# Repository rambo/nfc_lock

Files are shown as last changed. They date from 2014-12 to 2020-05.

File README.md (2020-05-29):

nfc_lock
========

(more) secure electric lock with DESFire EV1 NFC tags

## libnfc and libfreefare

    sudo apt-add-repository ppa:christopher-hoskin/ppa
    sudo apt-get update
    sudo apt-get install libnfc5 libnfc-bin libnfc-pn53x-examples libnfc-examples
    sudo apt-get install libfreefare0 libfreefare-bin
    sudo apt-get install python-zmq python-yaml python-tornado

`python-yaml` and `python-tornado` can be installed to virtualenv (esp tornado might be better to install via pip even if not to virtualenv the deb pulls unneccessary dependencies), zmq will be painful to install via pip, use the system package.

### For compiling

For the C programs.

    sudo apt-get install libfreefare-dev libnfc-dev libssl-dev pkg-config libzmq-dev

### RasPi

All libraries should be part of normal releases now.

## Terms

  - Card (PICC in NXP terms): The DESFire EV1 chip+antenna in a package (fob, card, sticker...)
  - Pre-Personalization step: Where card default master key is changed and applications are defined.
  - Application: collection of files on the card, application can have multiple keys for various purposes
  - Provisioning (or personalization) step: Where a personalized card is issued to a card holder and the card (plus backing datababase) is updated with relevant info
  - Diversified key: Key that has been derived from a master key via the method described in NXP AN19022

## SQLite for keys

Create a test file `sqlite3 keys.db`:

    CREATE TABLE valid_tokens (value TEXT UNIQUE, type INTEGER, acl INTEGER, external_ids TEXT);
    CREATE TABLE revoked_tokens (value TEXT UNIQUE, type INTEGER);

Prepare some tags and insert their (real) UIDs to the grants and revokes

    INSERT INTO revoked_tokens VALUES ("04453069b21e80");
    INSERT INTO valid_tokens VALUES ("04212f69b21e80", 0, 1);

In reality you will generate this file based on your person registry (keep track of validity times etc there, then regenerate the keydb for the door).

## Hacking

Remember to valgrind your C programs (`valgrind -v --leak-check=yes  myprog args`) at the same time as you do general functionality testing.

### RasPi

It seems Valgrind does not (and will not) support some instructions we use to talk with the NFC chips, see (this stackoverflow)[valgrindworkaround] for a workaround.

[valgrindworkaround]: http://stackoverflow.com/questions/20066215/valgrind-unrecognizes-memcmp-instruction-in-raspberry-pi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

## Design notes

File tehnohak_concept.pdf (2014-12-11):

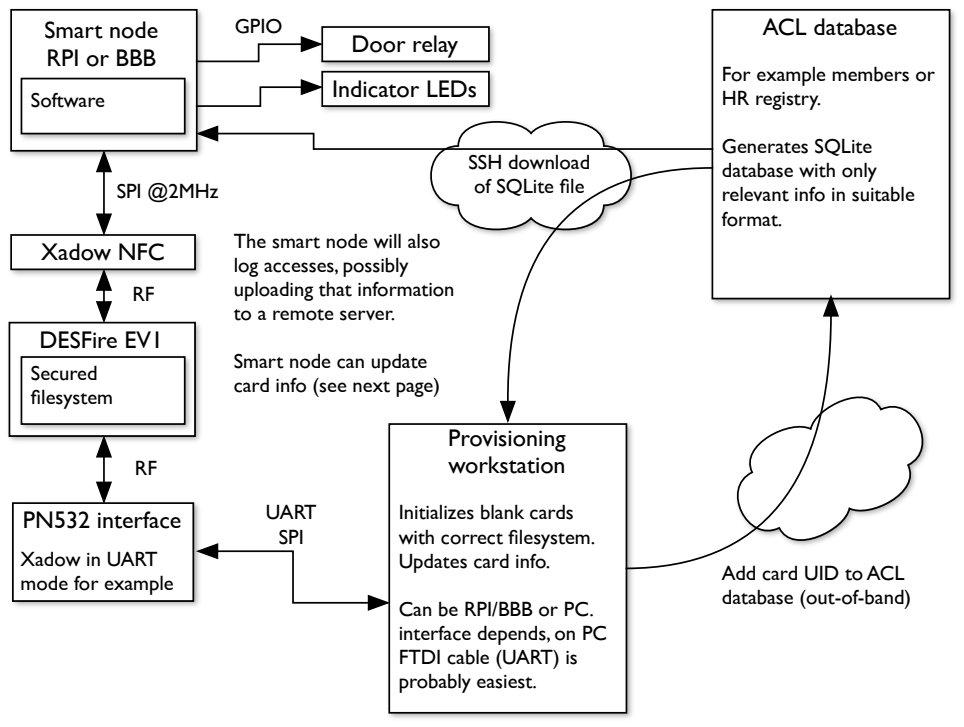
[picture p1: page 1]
Xadow NFC; SPI @2MHz; DESFire EV1 Secured filesystem; Door relay; GPIO; ACL database; Indicator LEDs; Provisioning workstation; UART SPI

Smart node
RPI or BBB
Software

For example members or
HR registry.

Generates SQLite
database with only
relevant info in suitable
format.

SSH download
of SQLite file

The smart node will also
log accesses, possibly
uploading that information
to a remote server.

Smart node can update
card info (see next page)

PN532 interface
Xadow in UART
mode for example

Initializes blank cards
with correct filesystem.
Updates card info.

Add card UID to ACL
database (out-of-band)

Can be RPI/BBB or PC.
interface depends, on PC
FTDI cable (UART) is
probably easiest.

# Card authentication

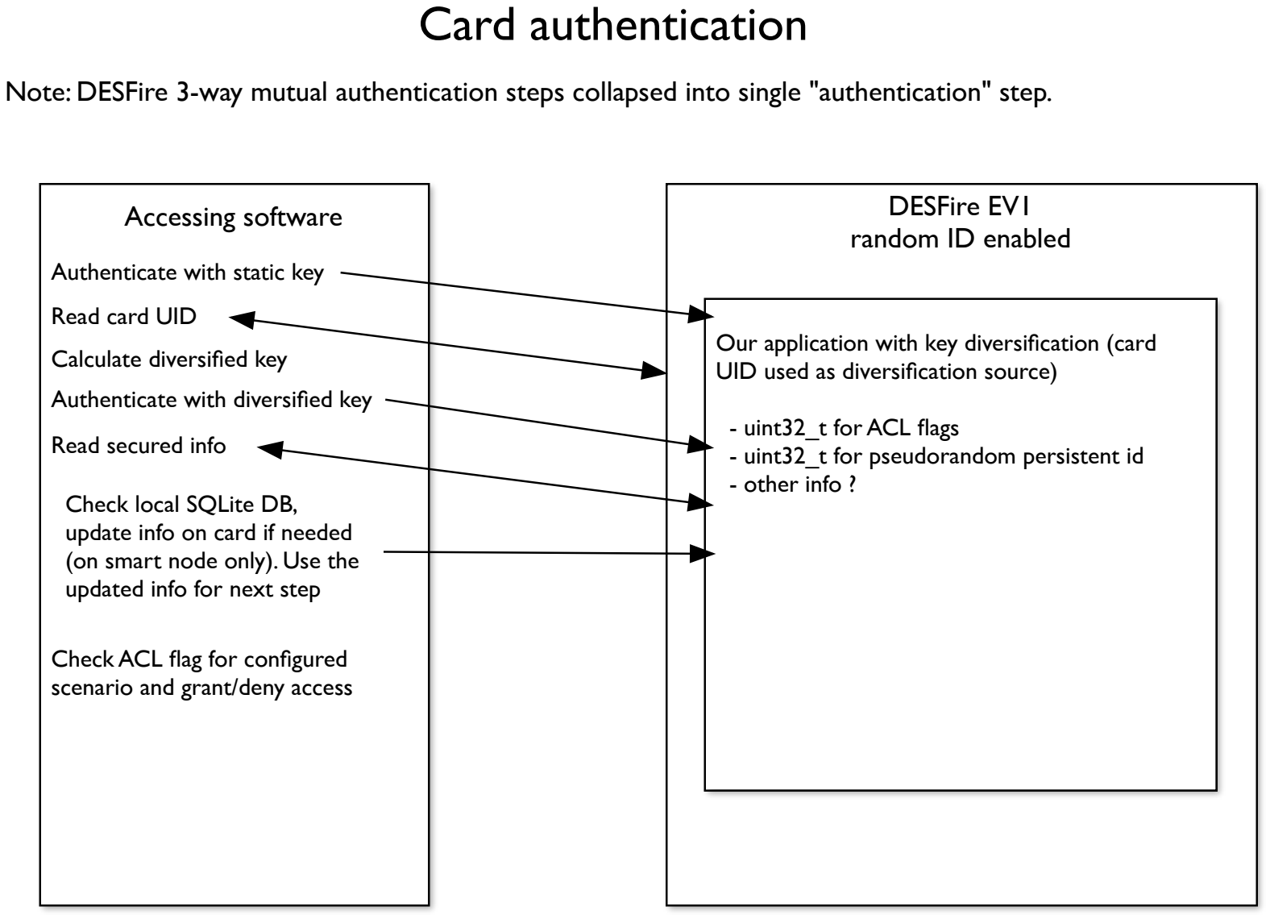
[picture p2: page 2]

Note: DESFire 3-way mutual authentication steps collapsed into single "authentication" step.

DESFire EV1
random ID enabled

Our application with key diversification (card UID used as diversification source)

- uint32_t for ACL flags
- uint32_t for pseudorandom persistent id
- other info ?

Accessing software

Authenticate with static key Read card UID
Calculate diversified key
Authenticate with diversified key Read secured info

Check local SQLite DB,
update info on card if needed (on smart node only). Use the updated info for next step

Check ACL flag for configured scenario and grant/deny access

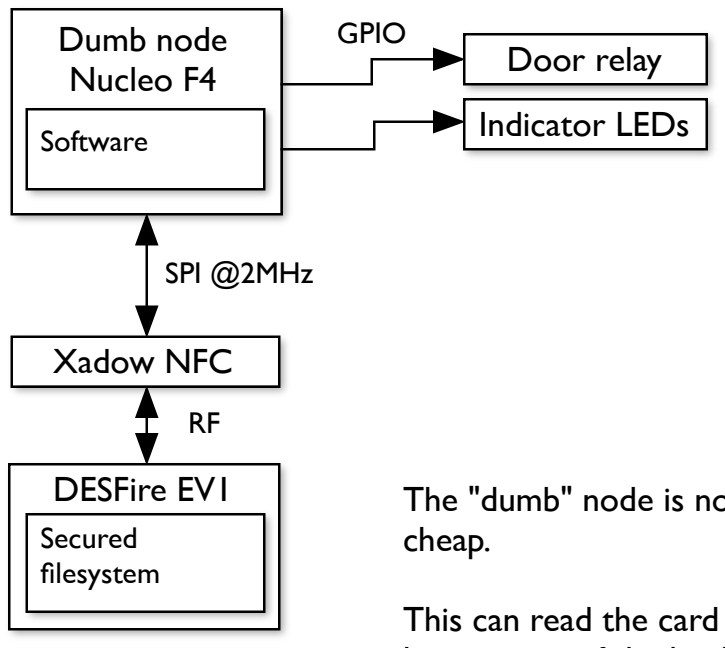
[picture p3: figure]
Dumb node Nucleo F4; Xadow NFC; SPI @2MHz; DESFire EV1; Software; Secured filesystem; Door relay; GPIO; Indicator LEDs; cheap.

The "dumb" node is not capable of running a full OS but the MCU is

This can read the card and check the ACL flag, but the node does not have a copy of the key/acl database or anything like that, it trusts that the smart node (which are at building entrances) will keep the flags updated.

It can do simple UDP broadcast of events (UID xxx granted/denied at node YYY) which the smart nodes can listen for (and log).

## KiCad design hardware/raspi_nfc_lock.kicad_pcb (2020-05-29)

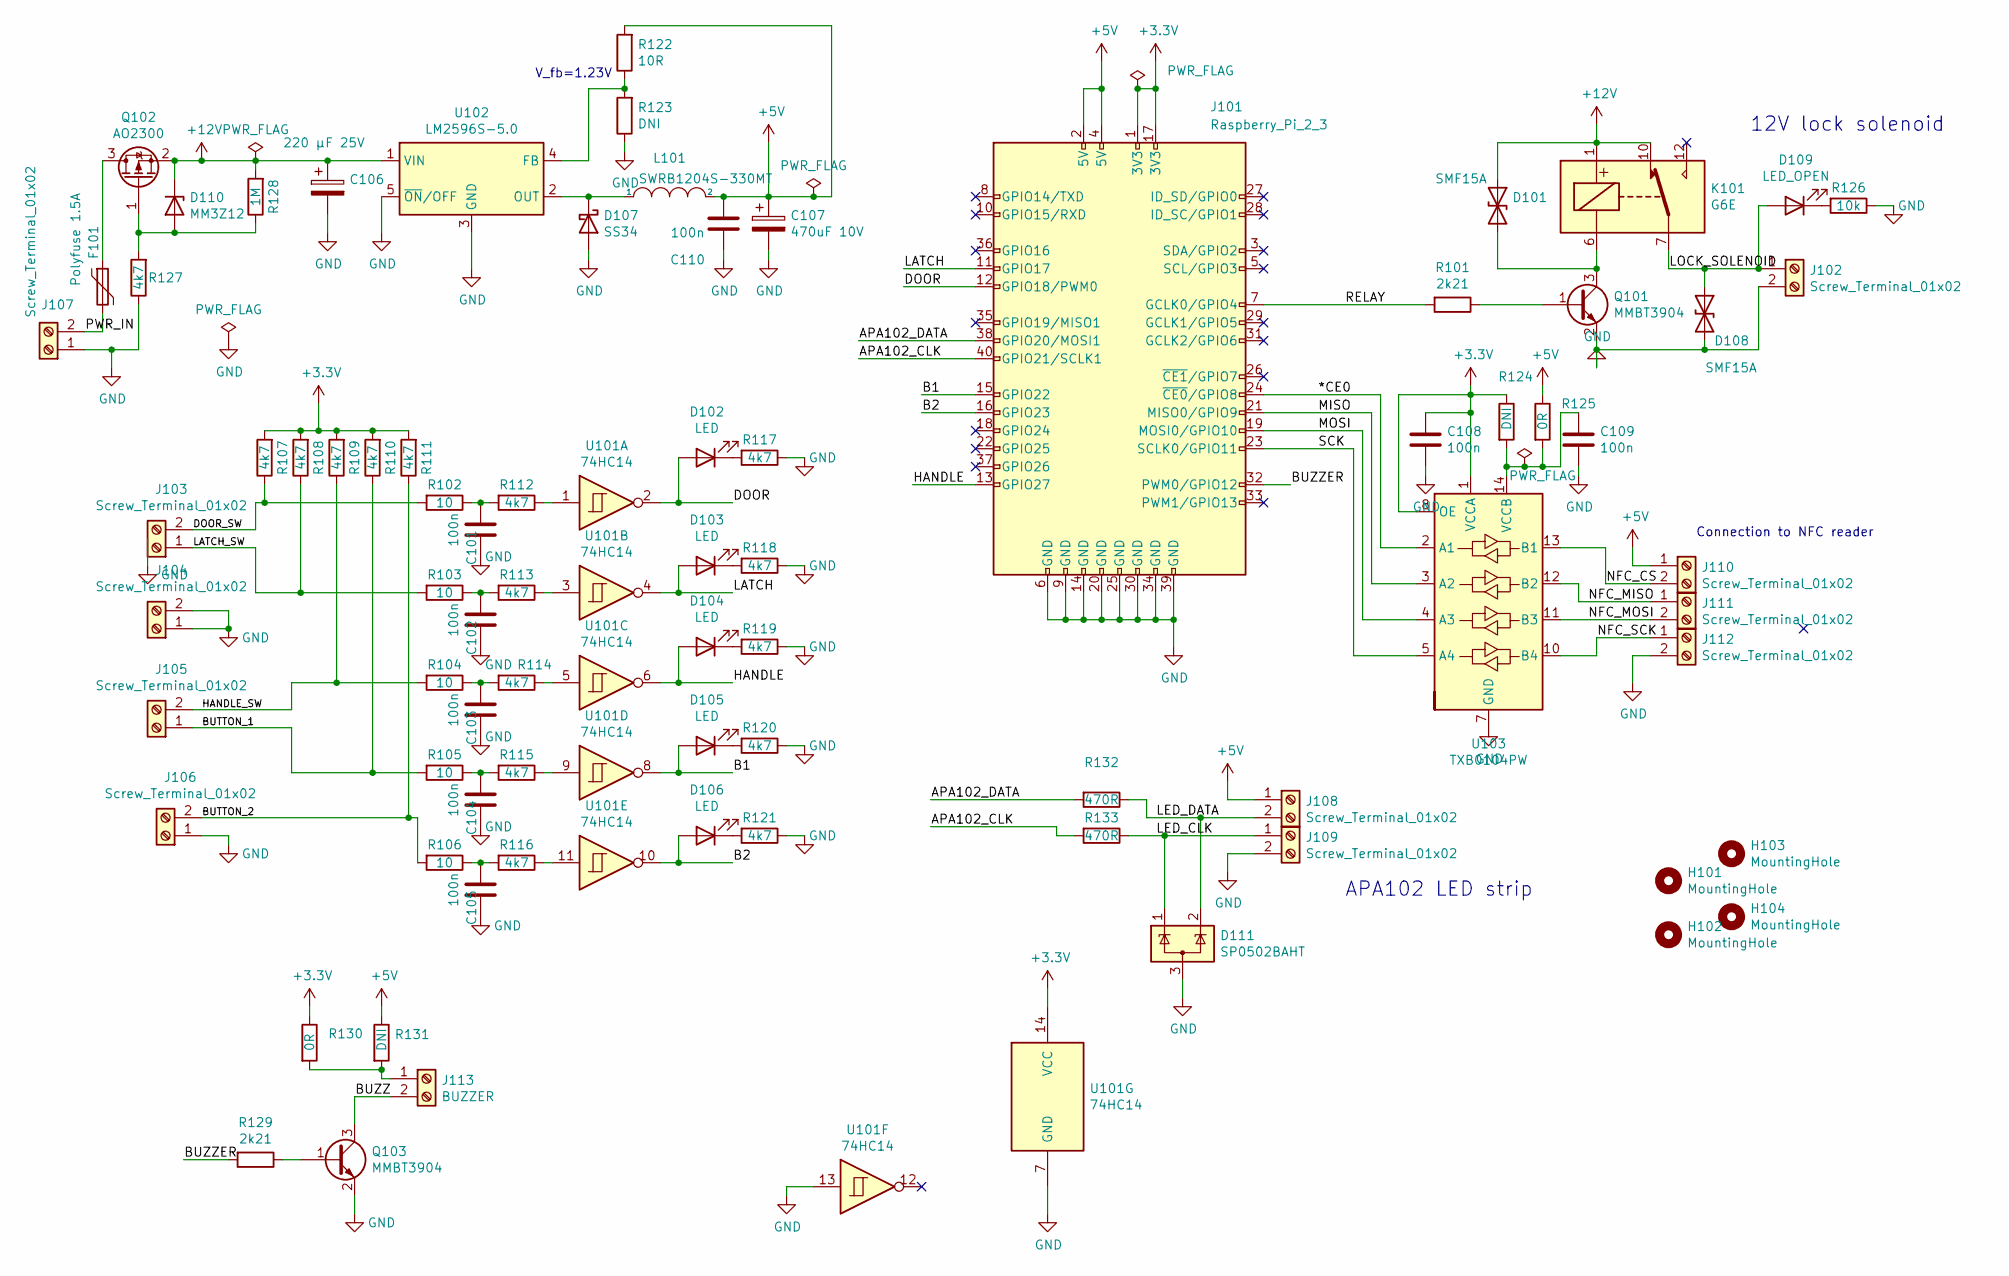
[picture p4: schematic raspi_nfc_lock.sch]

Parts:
C101, C102, C103, C104, C105, C108, C109: 100n; C_0603
C106: 220 μF 25V; CP_Elec_8x10
C107: 470uF 10V; CP_Elec_8x10.5
C110: 100n; C_1206
D101, D108: SMF15A; D_SOD-123
D102, D103, D104, D105, D106: LED; D_0603_1608Metric
D107: SS34; D_SMA
D109: LED_OPEN; D_0603_1608Metric
D110: MM3Z12; D_SOD-323
D111: SP0502BAHT; SOT-23
F101: Polyfuse 1.5A; Fuse_SMD2920
H101, H102, H103, H104: MountingHole; MountingHole_3.2mm_M3
J101: Raspberry_Pi_2_3; Pin_Header_Straight_2x20_Pitch2.54mm
J102, J103, J104, J105, J106, J107, J108, J109, J110, J111, J112: Screw_Terminal_01x02; TerminalBlock_Phoenix_MPT-0,5-2-2.54_1x02_P2.54mm_Horizontal
J113: BUZZER; TerminalBlock_Phoenix_MPT-0,5-2-2.54_1x02_P2.54mm_Horizontal
K101: G6E; Relay_SPDT_Omron_G6E
L101: SWRB1204S-330MT; L_12x12mm_H6mm
Q101, Q103: MMBT3904; SOT-23
Q102: AO2300; SOT-23
R101, R129: 2k21; R_0603
R102, R103, R104, R105, R106: 10; R_0603
R107, R108, R109, R110, R111, R112, R113, R114, R115, R116, R117, R118, R119, R120, R121, R127: 4k7; R_0603
R122: 10R; R_0603
R123, R124, R131: DNI; R_0603
R125, R130: 0R; R_0603
R126: 10k; R_0603
R128: 1M; R_0603
R132, R133: 470R; R_0603
U101: 74HC14; SOIC-14_3.9x8.7mm_P1.27mm
U102: LM2596S-5.0; TO-263-5_TabPin3
U103: TXB0104PW; TSSOP-14_4.4x5mm_P0.65mm

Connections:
+3V3: C108.1, J101.1 (3V3), J101.17 (3V3), R107.2, R108.2, R109.2, R110.2, R111.2, R124.1, R130.1, U101.14 (VCC), U103.1 (VCCA), U103.8 (OE)
+5V: C107.1, C110.2, J101.2 (5V), J101.4 (5V), J108.1, J110.1, L101.2, R122.2, R125.1, R131.1
+12V: C106.1, D101.1 (A1), D110.1 (K), K101.1, K101.10, Q102.2 (S), R128.2, U102.1 (VIN)
/*CE0: J101.24 (~CE0~/GPIO8), U103.2 (A1)
/APA102_CLK: J101.40 (GPIO21/SCLK1), R133.2
/APA102_DATA: J101.38 (GPIO20/MOSI1), R132.2
/B1: D105.2 (A), J101.15 (GPIO22), U101.8
/B2: D106.2 (A), J101.16 (GPIO23), U101.10
/BUTTON_1: J105.1, R105.2, R110.1
/BUTTON_2: J106.2, R106.2, R111.1
/BUZZ: J113.2, Q103.3 (C)
/BUZZER: J101.32 (PWM0/GPIO12), R129.2
/DOOR: D102.2 (A), J101.12 (GPIO18/PWM0), U101.2
/DOOR_SW: J103.2, R102.2, R107.1
/HANDLE: D104.2 (A), J101.13 (GPIO27), U101.6
/HANDLE_SW: J105.2, R104.2, R109.1
/LATCH: D103.2 (A), J101.11 (GPIO17), U101.4
/LATCH_SW: J103.1, R103.2, R108.1
/LED_CLK: D111.1 (K), J109.1, R133.1
/LED_DATA: D111.2 (K), J108.2, R132.1
/LOCK_SOLENOID: D108.1 (A1), D109.2 (A), J102.1, K101.7
/MISO: J101.21 (MISO0/GPIO9), U103.3 (A2)
/MOSI: J101.19 (MOSI0/GPIO10), U103.4 (A3)
/NFC_CS: J110.2, U103.13 (B1)
/NFC_MISO: J111.1, U103.12 (B2)
/NFC_MOSI: J111.2, U103.11 (B3)
/NFC_SCK: J112.1, U103.10 (B4)
/PWR_IN: F101.2, J107.2
/RELAY: J101.7 (GCLK0/GPIO4), R101.2
/SCK: J101.23 (SCLK0/GPIO11), U103.5 (A4)
GND: C101.1, C102.1, C103.1, C104.1, C105.1, C106.2, C107.2, C108.2, C109.2, C110.1, D107.2 (A), D108.2 (A2), D111.3 (A), J101.6 (GND), J101.9 (GND), J101.14 (GND), J101.20 (GND), J101.25 (GND), J101.30 (GND), J101.34 (GND), J101.39 (GND), J102.2, J104.1, J104.2, J106.1, J107.1, J109.2, J112.2, Q101.2 (E), Q103.2 (E), R117.1, R118.1, R119.1, R120.1, R121.1, R123.1, R126.1, R127.1, U101.7 (GND), U101.13, U102.3 (GND), U102.5 (~ON~/OFF), U103.7 (GND)
unnamed: C101.2, R102.1, R112.2
unnamed: C102.2, R103.1, R113.2
unnamed: C103.2, R104.1, R114.2
unnamed: C104.2, R105.1, R115.2
unnamed: C105.2, R106.1, R116.2
unnamed: C109.1, R124.2, R125.2, U103.14 (VCCB)
unnamed: D101.2 (A2), K101.6, Q101.3 (C)
unnamed: D102.1 (K), R117.2
unnamed: D103.1 (K), R118.2
unnamed: D104.1 (K), R119.2
unnamed: D105.1 (K), R120.2
unnamed: D106.1 (K), R121.2
unnamed: D107.1 (K), L101.1, U102.2 (OUT)
unnamed: D109.1 (K), R126.2
unnamed: D110.2 (A), Q102.1 (G), R127.2, R128.1
unnamed: F101.1, Q102.3 (D)
unnamed: J113.1, R130.2, R131.2
unnamed: Q101.1 (B), R101.1
unnamed: Q103.1 (B), R129.1
unnamed: R112.1, U101.1
unnamed: R113.1, U101.3
unnamed: R114.1, U101.5
unnamed: R115.1, U101.9
unnamed: R116.1, U101.11
unnamed: R122.1, R123.2, U102.4 (FB)

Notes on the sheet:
APA102 LED strip
12V lock solenoid
V_fb=1.23V
Connection to NFC reader

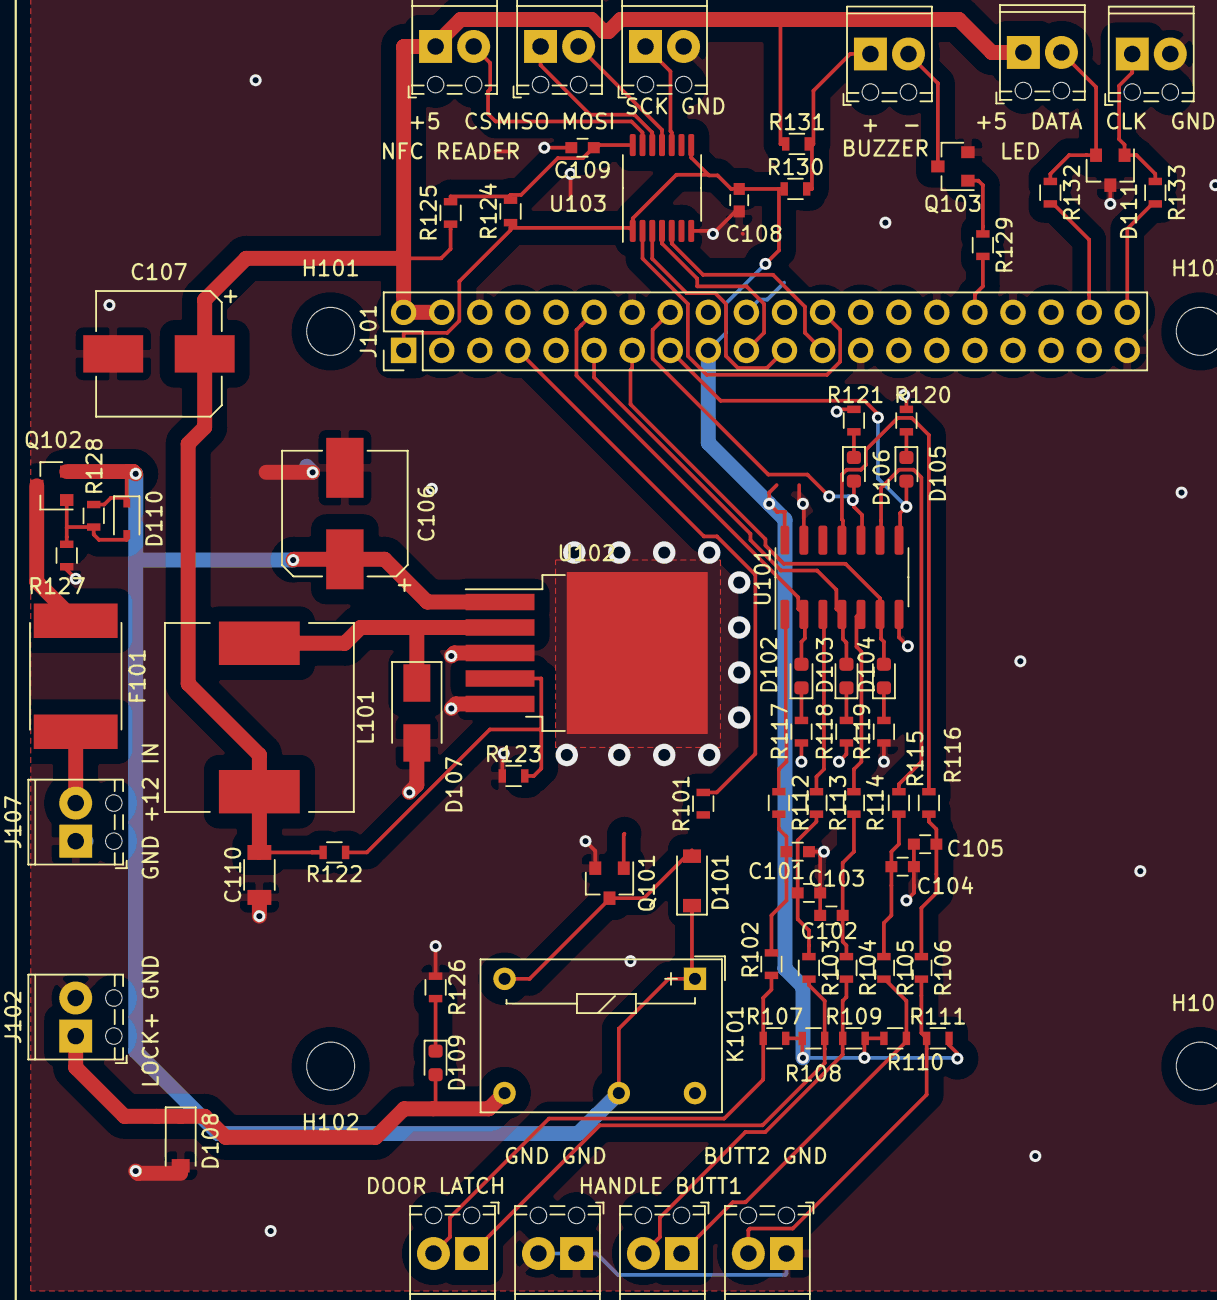
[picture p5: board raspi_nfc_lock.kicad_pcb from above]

Board: 2 copper layers, 80 parts (0 on the bottom side), 56 nets.

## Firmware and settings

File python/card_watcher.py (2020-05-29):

#!/usr/bin/env python3
# -*- coding: utf-8 -*-
import sys,os

import datetime
import yaml
import couchdb
import zmq
from zmq.eventloop.zmqstream import ZMQStream

# Reminder:  RPi.GPIO uses /dev/mem and requires root access, so that will not solve our GPIO issue
import usergpio

#usergpio.FAKE = True

class card_watcher(object):
    mainloop = None
    config_file = None
    config = {}
    zmq_context = None
    relay_disable_timer = None
    fobblogdb = None
    led_timer = None
    heartbeat_timer = None
    heartbeat_counter = 0
    relay_pin = None
    leds = None
    
    def __init__(self, config_file, mainloop):
        self.config_file = config_file
        self.mainloop = mainloop
        self.reload()
        print("Initialized")

    def leds_off(self, *args):
        # We get event info from the (possible) timer, that's why we need to accept more arguments even if we do not care about them
        self.leds.set_all_rgb(0,0,0)
        self.led_timer = None
        # To disable the timer that called this
        if self.led_timer:
            self.mainloop.remove_timeout(self.led_timer)
            self.led_timer = None
        return False

    def disable_relay(self, *args):
        # We get event info from the (possible) timer, that's why we need to accept more arguments even if we do not care about them
        self.relay.set(True)
        self.relay_disable_timer = None
        # To disable the timer that called this
        return False

    def hook_signals(self):
        """Hooks POSIX signals to correct callbacks, call only from the main thread!"""
        import signal as posixsignal
        posixsignal.signal(posixsignal.SIGTERM, self.quit)
        posixsignal.signal(posixsignal.SIGQUIT, self.quit)
        posixsignal.signal(posixsignal.SIGHUP, self.reload)

    def log(self, card_uid, card_valid):
        if not self.fobblogdb:
            self.reconnect_couchdb()
            if not self.fobblogdb:
                return False

        try:
            return self.fobblogdb.save({
                "card_uid": card_uid,
                "card_valid": card_valid,
                "timestamp": datetime.datetime.now().strftime("%Y-%m-%d %H:%M:%S.%f"),
                "action": self.config['log']['action'],
            })
        except Exception as e:
            # TODO: catch couchdb/socket errors only
            print("log: got e=%s" % repr(e))
            return False

    def reconnect_couchdb(self):
        self.fobblogdb = None
        try:
            couch = couchdb.Server(self.config['log']['server'])
            self.fobblogdb = couch[self.config['log']['db']]
        except Exception as e:
            # TODO: catch socket errors only
            print("reconnect_couchdb: got e=%s" % repr(e))

    def reload(self, *args):
        with open(self.config_file) as f:
            self.config = yaml.load(f, Loader=yaml.SafeLoader)

        self.reconnect_couchdb()

        # Init relay GPIO
        self.relay = usergpio.gpiopin(4, dir="out")
        self.relay.set(True)

        # Turn the LEDs off (and init the gpio for them)
        self.leds = usergpio.ledstring(data_pin=self.config['leds']['datapin'],
                                       clk_pin=self.config['leds']['clkpin'],
                                       n=self.config['leds']['n'])
        self.leds.set_all_rgb(10,10,10)
        self.led_timer = self.mainloop.call_later(self.config['leds']['error']['time'], self.leds_off)

        if self.zmq_context:
            self.zmq_context.destroy()
            self.zmq_context = None
        self.zmq_context = zmq.Context()
        self.zmq_socket = self.zmq_context.socket(zmq.SUB)
        self.zmq_socket.connect(self.config['gatekeeper_socket'])
        #subscribe all topics
        self.zmq_socket.setsockopt(zmq.SUBSCRIBE, b'')
        self.zmq_stream = ZMQStream(self.zmq_socket)
        self.zmq_stream.on_recv(self._on_recv)

        self.start_heartbeat()
        print("Config (re-)loaded")

    def _on_recv(self, packet):
        topic = packet[0].decode('ascii')
        data = packet[1:]

        print("_on_recv topic=%s, data=%s" % (topic, repr(data)))

        if topic == "OK":
            self.valid_card_seen(data[0].decode('ascii'))
            return

        # Other results are failures
        print("Card %s not valid (reason: %s)" % (data[0], topic))
        self.leds.set_all_rgb(255,0,0)
        self.led_timer = self.mainloop.call_later(self.config['leds']['error']['time'], self.leds_off)

        self.log(data[0].decode('ascii'), topic)

    def valid_card_seen(self, card_uid):
        print("Card %s valid, activating relay for %d seconds" % (card_uid, self.config['relay']['time']))
        if self.relay_disable_timer:
            self.mainloop.remove_timeout(relay_disable_timer)
        self.relay.set(False)
        self.mainloop.call_later(self.config['relay']['time'], self.disable_relay)

        #LED indication
        self.leds.set_all_rgb(0,255,0)
        self.led_timer = self.mainloop.call_later(self.config['leds']['ok']['time'], self.leds_off)

        self.log(card_uid, "OK")

    def _get_heartbeat_time(self):
        k = self.heartbeat_counter % len(self.config['leds']['heartbeat']['time'])
        return (self.config['leds']['heartbeat']['time'][k])

    def start_heartbeat(self):
        self.heartbeat_counter = 0
        self.leds.setstr("w")
        self.heartbeat_timer = self.mainloop.call_later(1, self.heartbeat_callback)

    def heartbeat_callback(self, *args):
        self.heartbeat_counter += 1

        #If LEDs are not reserved, blink HB
        if not self.led_timer:
            if (self.heartbeat_counter % 2):
                #odd numbers mean it's turn-off time
                self.leds.setstr("w......")
            else:
                self.leds.setstr(".......")
                
        self.heartbeat_timer = self.mainloop.call_later(self._get_heartbeat_time(), self.heartbeat_callback)
        # TODO: we should probably zero out the hearbeat counter every once in a while
        if self.heartbeat_counter >= len(self.config['leds']['heartbeat']['time']):
            self.heartbeat_counter = 0

    def quit(self, *args):
        # This will close the sockets too
        if self.zmq_context:
            self.zmq_context.destroy()
        self.mainloop.stop()

    def run(self):
        print("Starting mainloop")
        self.mainloop.start()



if __name__ == '__main__':
    if len(sys.argv) < 2:
        print("Usage: card_watcher.py config.yml")
        sys.exit(1)
    #TODO: init GPIO and do seteuid() to non-root account after that
    from tornado import ioloop
    loop = ioloop.IOLoop.instance()
    instance = card_watcher(sys.argv[1], loop)
    instance.hook_signals()
    try:
        instance.run()
    except KeyboardInterrupt:
        instance.quit()

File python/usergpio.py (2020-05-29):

import os
import time
import struct

class gpiopin(object):
    _filename = None
    _fh = None
    _pin = None
    _inverted = False


    def __init__(self, pinnumber, dir="in", inverted=False):
        iodir = "/sys/class/gpio"
        self._filename = f"{iodir}/gpio{pinnumber}"
        #Export pin if not there
        if not os.path.isfile(f"{iodir}/gpio{pinnumber}/direction"):
            with open(f"{iodir}/export", "w") as f:
                f.write("%d\n" % pinnumber)
        with open(f"{iodir}/gpio{pinnumber}/direction", "w") as dirfile:
            dirfile.write(f"{dir}\n")
        if dir == "in":
            self._fh = open(f"{iodir}/gpio{pinnumber}/value", "rb", 0)
        else:
            self._fh = open(f"{iodir}/gpio{pinnumber}/value", "wb", 0)
        self._pin = pinnumber
        self._inverted = inverted

    def __del__(self):
        if self._fh:
            self._fh.close()
        
    def set(self, state):
        state = state^self._inverted
        if state:
            self._fh.write(b'1')
        else:
            self._fh.write(b'0')

    def get(self):
        self._fh.seek(0)
        if int(self._fh.read())^self._inverted:
            return 0
        return 1

RGBTABLE = {
    'R': [200, 0, 0],
    'r': [40, 0, 0],
    'G': [0, 255, 0],
    'g': [0, 60, 0],
    'B': [0, 0, 255],
    'b': [0, 0, 60],
    'y': [60, 40, 0],
    'Y': [255, 200, 0],
    'M': [200, 0, 255],
    'm': [40, 0, 60],
    'W': [255, 255, 255],
    'w': [60, 60, 60],
    ' ': [0,0,0],
    '.': [0,0,0]
}

class ledstring(object):
    _clkpin = None
    _datapin = None
    _nleds=1

    def __init__(self, data_pin=20, clk_pin=21, n=1):
        self._clk = gpiopin(clk_pin, "out")
        self._data = gpiopin(data_pin, "out")
        self._nleds = n

    def _out(self, data):
        for outbyte in data:
            for bit in range(7,-1,-1):
                self._clk.set(0)
                d=((outbyte&(1<<bit))>>bit)
                self._data.set(d)
                self._clk.set(1)
        self._clk.set(0)

    def _send_rgb(self,r,g,b):
        current = 16 #out of 31
        #Send global current + 3 PWM values with 0b111 starting bits
        self._out(struct.pack("BBBB", 224+current, b, g, r))

    def _start_of_frame(self):
        self._out(b"\x00\x00\x00\x00")

    def _end_of_frame(self):
        self._out(b"\xff\xff\xff\xff")
        
    def set_all_rgb(self, r,g,b):
        self._start_of_frame()
        for ledno in range(self._nleds):
            self._send_rgb(r,g,b)
        self._end_of_frame()
        self._start_of_frame()
        self._start_of_frame()

    #Sets LEDs with string like "RRRGGGBBB"
    def setstr(self, colors):
        self._start_of_frame()
        for c in colors:
            self._send_rgb(RGBTABLE[c][0], RGBTABLE[c][1], RGBTABLE[c][2])
        self._end_of_frame()
        #self._start_of_frame()
        #self._start_of_frame()

if __name__ == "__main__":
    relay = gpiopin(4, dir="out")
    buzzer = gpiopin(12, dir="out")
    led_clk = gpiopin(20, dir="out")
    led_data = gpiopin(21, dir="out")
    latch = gpiopin(17, dir="in")
    door = gpiopin(18, dir="in")
    b1 = gpiopin(22, dir="in")
    b2 = gpiopin(23, dir="in")
    handle = gpiopin(27, dir="in")
    
    for i in range(100):
        relay.set(0)
        #buzzer.set(0)
        time.sleep(0.5)
        relay.set(1)
        #buzzer.set(1)
        time.sleep(0.5)

        print(f"latch={latch.get()} door={door.get()} handle={handle.get()} b1={b1.get()} b2={b2.get()}")
        

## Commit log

2014-10-25 some notes about which keys are needed where
    [nfc_lock_keys_needed.ods]
2014-10-25 open the first libnfc configure device and print info
2014-10-25 notes about Raspberry Pi
2014-10-26 handle the relay too, refactor the teardown on interrupt
2014-10-26 rename the interrupt channel
2014-10-26 use the default device
2014-10-26 print tag id and application id as hex and decimal
2014-11-08 the canonical GPIO test cocode, LED blinker
2014-11-09 started writing the actual relay controlling program, based on the test_gpio.go
2014-11-11 moving these relay control outside the tag checking does not help with the memory-issue
2014-11-15 switching to uint32 for ACL seems to work fine... go figure...
2014-11-15 after a couple of succesfull reads I now keep getting "unknown error" when re-authenticatingwith the ACL-read key (either key diversification gets fscked or something goes wrong in libfreefare
2014-11-15 note about the GPIO timers
2014-11-15 opening the device works if I give the connstring from cli, the default "" does not...
2014-11-15 scan for devices if none is given on cli, something in the scan leaks memory btw...
    Using device pn532_uart:/dev/ttyUSB0
    ==7746==
    ==7746== HEAP SUMMARY:
    ==7746== in use at exit: 1,736 bytes in 5 blocks
    ==7746== total heap usage: 516 allocs, 511 frees, 49,427 bytes
    allocated
    ==7746==
    ==7746== Searching for pointers to 5 not-freed blocks
    ==7746== Checked 169,904 bytes
    ==7746==
    ==7746== LEAK SUMMARY:
    ==7746== definitely lost: 0 bytes in 0 blocks
    ==7746== indirectly lost: 0 bytes in 0 blocks
    ==7746== possibly lost: 0 bytes in 0 blocks
    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
2014-11-15 print out what we actually parsed as the aid bytes
2014-11-16 print the parsed sysid
2014-11-16 print the intermediate key bytes for debugging
2014-11-16 this is the correct way to clean up timed out thread, it seems...
2014-11-24 loop and use correct receive method
    [req_test.py]
2014-11-24 check the received UID and respond with correct code
    [keyserver.py]
2014-11-25 output messages from ZMQ only in case of trouble
2014-11-28 bind to pubsub socket, refactor string sending to a helper
2014-11-28 I have to handle the ZMQ messages in the tag handler thread... this compiles but the socket is not passed on correctly
2014-11-28 fix the socket passing, use standard string as topic
2014-11-28 use the result as topic, close the socket we failed to open before terminating the context or zmq hangs...
2014-12-01 bypass couchdb problems on startup
    [card_watcher.py]
2014-12-01 bypass couchdb errors when logging
    [card_watcher.py]
2014-12-01 remove old properties, fix the timers from gobject to tornado
    [card_watcher.py]
2014-12-03 small breakout for three status leds
    [three_led_breakout.brd, three_led_breakout.sch]
2014-12-05 remember to start these timers too...
2014-12-08 make less noise, package the requirements file too
    [card_watcher.py, keyserver.py]
2014-12-09 make a separate program for formatting the card (de-personalize)
2014-12-09 print the errors
2014-12-09 printing errors
2014-12-11 got tired of trying to figure out why it dies, just unroll the function...
2014-12-11 print the tag info
2014-12-11 updated the table telling where various keys are needed
    [nfc_lock_keys_needed.ods]
2015-01-15 logging helpers (TODO: switch output from all other programs to use these)
2015-02-18 it seems that for UPiS NO is the new NC, and we have to use external relay...
2015-03-24 switch to the log helpers for output
2020-05-20 Updated ZMQ calls to current version
2020-05-24 New GPIO module with APA102 LED string support
2020-05-24 Added RPi shield that contains connections and power supply
    [raspi_nfc_lock.kicad_pcb, raspi_nfc_lock.sch, three_led_breakout.brd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]
